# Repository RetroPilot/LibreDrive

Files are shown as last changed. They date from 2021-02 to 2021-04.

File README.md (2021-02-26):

# LibreDrive
OpenSource automation system for pre-autonomous vehicles

## Want to help development?

1. Check the Issues https://github.com/RetroPilot/LibreDrive/issues
2. If your issue or feature/work request doesn't exist, create it
3. Issue will be assigned to developer
4. Issue will be triaged and added to project board for visibility
5. Add all progress comments to issue directly

**MOST IMPORTANTLY:**

When your issue is completed, it shouldn't be closed until you update the documentation in appropriate directory

If you do not want to write documentation, ping @amzoo and he will assist

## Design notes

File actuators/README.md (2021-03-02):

# Actuators
Development around automating driver input

## FAQ

### Why use stepper motors?

[@dzid_ Stepper Motor Selection](https://docs.google.com/spreadsheets/d/1i-fc_-HzTeXHEhWJxIY2qmCmWLXJygV-4YG03bAaAyE/edit#gid=0)

Pros
- Low speed high torque
- Standard NEMA frame mounting
- Wide range of geared/non-geared options
- Wide range of libraries/controllers to use

Cons
- Gearing needed to get higher speed requirements
- Stepping control isn't necessary as external encoders are used

### Why use BLDC (Brushless DC) motors?

[ODrive Brushless Motor Selection](https://docs.google.com/spreadsheets/d/12vzz7XVEK6YNIOqH0jAz51F5VUpc-lJEs3mmkWP1H4Y/edit#gid=0)

Pros
- High speed low torque
- Smooth operation
- Many options from the hobby RC drone/airplane world
- Custom motors are available without breaking the bank

Cons
- Gearing needed to get higher torque requirements
- Back driving through larger gear ratios becomes more difficult

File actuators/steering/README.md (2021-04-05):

# Steering Acutator
General documentation for development surrounding the steering actuator

## Requirements
Note: ** double asterisks mark soft requirements that can be changed. This allows us
to determine other requirements in order to move on with a design

General
- ** Under $150 for complete BOM
  
Mechanical
- Peak Torque: ~5 Nm (needs verification)
- Peak Rate: 400 deg/s
- ** 300mm OD Driven Ring
- ** 18mm OD Drive Gear

Electrical
- ** Estimated Power: ~25W
- ** Input Voltage: 12V
- ** Estimated Current: 2.9A

Human Centric
- Does not interfere with drivers hands
- Able to be over-powered and software shutdown after sustained input force

Go Home Specification

1. The system should be able to detect and report user inputs

    1.1 User input torque (angle rate vs current motor voltage)

    1.2 Steering wheel angle

2. The system should be able to detect and report errors

    - 2.1 Motor failures
        - 2.1.1 jam
        - 2.1.2 disconnected
    - 2.2 Firmware check fail
    - 2.3 Bus failures
        - 2.3.1 CAN checksum
        - 2.3.2 CAN message timeout
        - 2.3.3 request exceeds limits
3. The system should not override user inputs
    - 3.1 The motor should supply a torque vector towards zero at the torque required to overcome static friction within the actuator
        - 3.1.1 this will emulate true freewheeling, allowing the vehicle's power steering system to center the wheel as normally installed
        - 3.1.2 this torque requirement can be found programmatically before installation. it should be directly proportional to a voltage value if we use SimpleFOC
        - 3.1.3 reasonable static friction should not be very high, but we can make a very low estimate here
    - 3.2 If the motor is consuming more energy than expected, the motor relays will disengage allowing the motor to freewheel
        - 3.2.1 in this fail state, reporting is still enabled and the status code is communicated to the user
        - 3.2.2 the expected energy map will be created for static friction of actuator +1Nm during the validation phase and burned into memory
    - 3.3 A  physical disconnect will be implemented to detach the motor from the driven assembly
        - 3.3.1 possibly solenoid clutches - if we use these we can add another check / error state for them

## Subcomponents / TODO

- Microcontroller selection

    - STM32F205

- PCB design

    - Physical dimensions / layout
    - Power supply

- Motor selection

    - Type, specifications

- Angle sensor / position feedback

    - Theory of operation

- User override detection

    - Theory of operation

- Firmware

    - CAN I/O specification
    - Motor control algorithm
    - Go home mode specification
    - Self-testing and error reporting
    - Safety

- Mechanical Design

    - Mechanical specifications
    - Gearing for motor / actuation
    - Gearing for angle sensor
    - Column mount
    - Wheel mount system

## Models

### Full Stupid

Full Stupid Honda

- Contributors: smurf
- Status: WIP
- [Link to Files](https://github.com/RetroPilot/full-stupid/tree/master)

### retropilot-drivetronik

- Contributors: wocsor
- Status: WIP, tested actuaton on 2003 Toyota Celica
    - [Video](https://youtu.be/OpUxE-Uwttc)
- [Link to Files](https://github.com/wocsor/retropilot-drivetronik)

### Second model 

- Contributors: amzoo
- Status: WIP
- Link:

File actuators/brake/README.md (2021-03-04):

# Brake Acutator
General documentation for development surrounding the brake actuator

## Requirements
Note: ** double asterisks mark soft requirements that can be changed. This allows us
to determine other requirements in order to move on with a design

General
- ** Under $150 for complete BOM

Mechanical
- Can exert 700N a distance of 50mm (resolution 2mm) to end of brake pedal
- Emergency mechanical release decouples actuator from pedal
- Can withstand human input of 2500N
- Does not restrict pedal's full range of motion

Electrical

Option 1: 700N, 0.3s actuation time, 50mm travel
- Estimated Power: ~120W
- ** Input Voltage: 12V
- ** Estimated Current: 10A

Option 2: 700N, 0.6s actuation time, 50mm travel
- Estimated Power: ~60W
- ** Input Voltage: 12V
- ** Estimated Current: 5A

Option 3: 350N, 0.3s actuation time, 50mm travel
- Estimated Power: ~42W
- ** Input Voltage: 12V
- ** Estimated Current: 3.5A

Option 3: 350N, 0.6s actuation time, 50mm travel
- Estimated Power: ~21W
- ** Input Voltage: 12V
- ** Estimated Current: 1.75A

## Subcomponents / TODO

- Microcontroller selection
    - STM32

- PCB design

    - Physical dimensions / layout
    - Power supply

- Motor selection

    - Type, specifications

- Pedal throw sensor

    - angle sensor at fulcrum of pedal lever + magnet

- User override detection

    - strain gauge / pressure sensor on pedal surface
    - emergency release state detection

- Firmware

    - CAN I/O specification
    - Motor control algorithm
    - Go home mode specification
    - Self-testing and error reporting
    - Safety

- Mechanical Design

    - Mechanical specifications
    - Gearing for motor / actuator unit
    - Sensor package mount on pedal surface
    - Actuator unit mount
    - Emergency physical release mechanism

## Models

### Clippy on the Brakey

- Contributors: amzoo
- Status: WIP
- Link: 

### Second model 

- Contributors: amzoo
- Status: WIP
- Link:

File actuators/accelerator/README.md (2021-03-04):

# Accelerator Acutator
General documentation for development surrounding the accelerator actuator

## Requirements
Note: ** double asterisks mark soft requirements that can be changed. This allows us
to determine other requirements in order to move on with a design

Accelerator Types
- Electronic Drive by Wire
- Cable Driven Throttle Body

General
- Under $150 for complete BOM
- Does not restrict pedal's full range of motion

## Models

### Clippy on the Zoomy

- Contributors: amzoo
- Status: WIP
- Link: 

### Second model 

- Contributors: amzoo
- Status: WIP
- Link:

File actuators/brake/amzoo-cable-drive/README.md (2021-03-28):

# Cable Driven Actuator
Pulley and housing for driving brake cables for a remote pulling actuator

## Status
This is still WIP. Parts will be added as they are tested, meaning that the print 
files that live here have been tested by amzoo

## Subcomponents / TODO

- Firmware

    - (TESTING) SimpleFOC on Bigtreetech S57B STM32 board

- Mechanical Design
    - (DONE) Motor to cable pulley/housing
    - Cable to pedal attachment
    - Pedal press sensor
    - Pedal travel sensor
    - Actuator to floor mount
    - Cable end to floor mount

## Assembly Instructions

WIP

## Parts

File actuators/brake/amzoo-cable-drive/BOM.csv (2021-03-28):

Category | Description | Notes | Qty | Price | Link
Printed Components
 | Pulley Housing |  | 1
 | Pulley Housing Lid |  | 1
 | Pulley |  | 1
OTS Components
 | NEMA 23 15:1 Stepper Motor | Gear ratio may be off. Currently having issues driving motor fast enough. Likely a FW issue with 8bit controller. Calculations should work on this. | 1 | $73.00 | amazon.com/gp/product/B00WAV0N5E/ref=ppx_yo_dt_b_asin_title_o05_s00?ie=UTF8&psc=1
 | 12mm Bore Hub Flange |  | 1 | $16.00 | amazon.com/gp/product/B07QS6PGKB/ref=ppx_yo_dt_b_asin_title_o05_s01?ie=UTF8&psc=1
 | Bicycle Brake Cable/Housing | Need any two brake cables with Barrel Style ends. DO NOT use shifter cables, they are not rated for the required loads. Other options exist from off-brand sources | 1 | $12.00 | amazon.com/gp/product/B0050LUBZ8/ref=ppx_yo_dt_b_asin_title_o06_s00?ie=UTF8&psc=1
OTS Hardware
 | BHCS M4 x 16mm | Connects hub to printed pulley | 4
 | SHCS M5 x 10mm | Connects pulley housing to stepper motor | 4
 | BHCS M3 x 20mm | Connects pulley housing lid to housing | 5

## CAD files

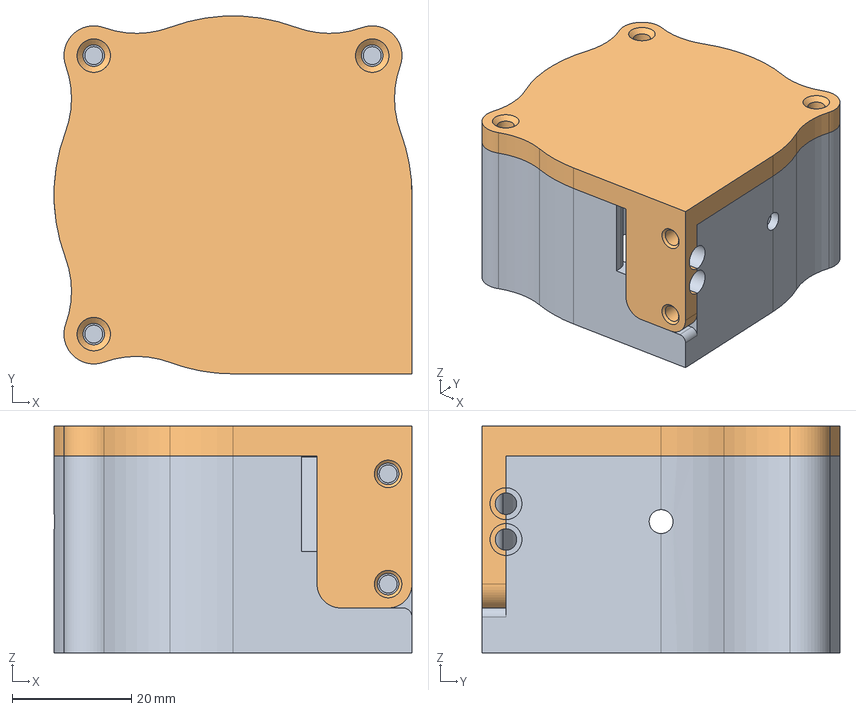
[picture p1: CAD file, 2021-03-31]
actuators/brake/amzoo-cable-drive/cad-files/PulleyHousingLidAsm.step
60.0 x 60.0 x 38.0 mm

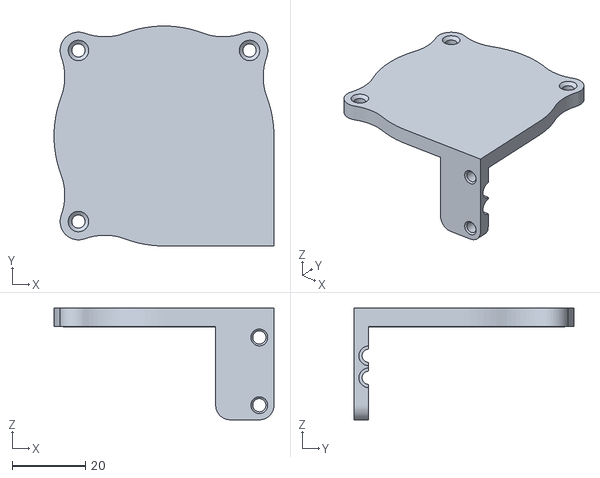
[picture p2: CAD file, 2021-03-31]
actuators/brake/amzoo-cable-drive/print-files/PulleyLid.stl
60.0 x 60.0 x 30.5

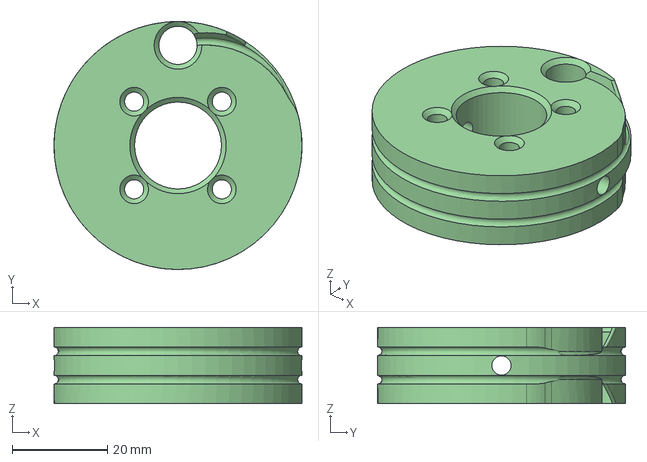
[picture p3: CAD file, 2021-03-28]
actuators/brake/amzoo-cable-drive/cad-files/Pulley.step
52.0 x 52.0 x 16.0 mm

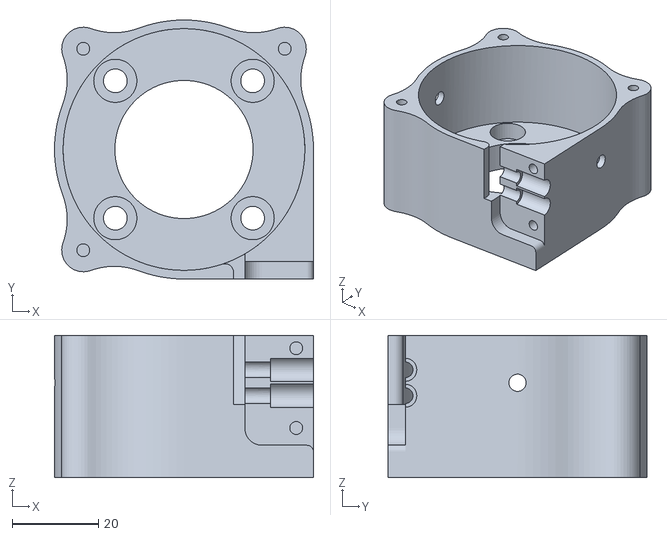
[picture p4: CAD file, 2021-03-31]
actuators/brake/amzoo-cable-drive/print-files/PulleyHousing.stl
60.0 x 60.0 x 33.0

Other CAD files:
actuators/brake/amzoo-cable-drive/print-files/Pulley.stl

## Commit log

2021-02-28 Adding full-stupid model to steering actuators
    [6368-retainer-v0.obj, CE3_clamp-inner-outer-v03-160mm-rad-10deg.3mf, CE3_clamp-inner-v03-160mm-rad-10deg.3mf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]
2021-02-28 removing full-stupid directory to add back in as submodule
    [6368-retainer-v0.obj, CE3_clamp-inner-outer-v03-160mm-rad-10deg.3mf, CE3_clamp-inner-v03-160mm-rad-10deg.3mf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]
2021-02-28 Update brake requirements
2021-03-01 added wocsor steer actuator as a submodule
2021-03-01 update steering readme and add subcomponents
2021-03-01 added FAQ to actuators
2021-03-02 Added more requirements to steering and brake actuators
2021-03-03 Added motor calculations for steering actuator
2021-03-03 Added pedal calcs to motor_selector
2021-03-04 add subcomponents to brake actuator
2021-03-16 adding steering toggle clamp
2021-03-16 Update microcontroller selection to STM32F205
2021-03-28 Added first files for cable pulley and housing
    [BOM.csv, Pulley.step, Pulley.stl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]
2021-03-31 Updating models to fix lid print issues
    [PulleyHousing.stl, PulleyHousingLid.stl, PulleyHousingLidAsm.step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]
2021-04-05 add go home spec to steering readme
